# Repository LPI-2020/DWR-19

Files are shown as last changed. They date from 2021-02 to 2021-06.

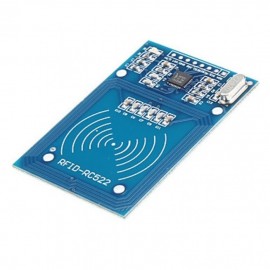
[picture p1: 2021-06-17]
01Relatorios/VariosCapitulosRelatorio/Fotos-Material/leitor-rfid-arduino.jpg

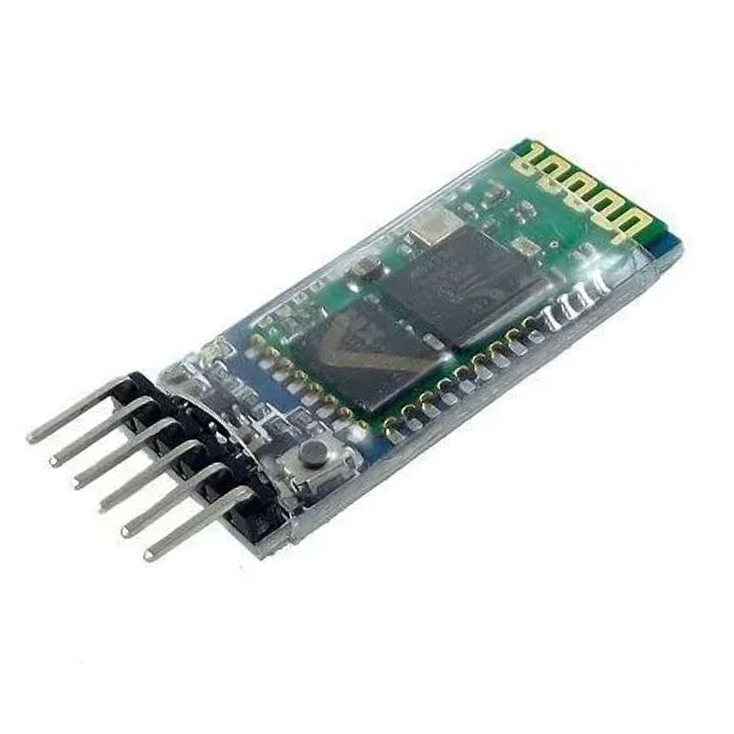
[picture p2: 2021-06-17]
01Relatorios/VariosCapitulosRelatorio/Fotos-Material/modulo_bluetooth_hc_05_mestre_escravo_341_1_20200806213305.jpg

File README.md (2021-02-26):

# Digital Waiter Robot (DWR -19)

Developed in:
- Projeto Integrador - LPI II (2021)

Members:
- Bruno Miguel Vasconcelos da Silva, a88289
- Diogo Miguel Cunha Fernandes, a88262
- Duarte Miguel Novo Rodrigues, a88259
- Francisco Lopes Salgado, a88231 
- João Pedro Dias Miranda, a88237
- José Tomás Lima de Abreu, a88218

Directed by:
- Luís André Magalhães de Barros

Short description (PT):
- A ideia do produto surgiu da necessidade de atuar perante o panorama pandémico (Covid-19), mais propriamente no auxílio a pessoas que se encontrem em isolamento.
- Uma pessoa em isolamento não pode ter contacto com o mundo exterior. Por este motivo, pensou-se em desenvolver um robô que faça chegar bens essenciais à pessoa em isolamento.
-	A função principal do produto será desempenhar o papel de um “empregado de mesa”, daí o nome “Waiter”. O termo “Digital” advém do facto de todas funcionalidades serem maioritariamente implementadas de forma digital, perfazendo o nome do robô “Digital Waiter Robot”.

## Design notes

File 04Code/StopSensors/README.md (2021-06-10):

# Stop Sensors:
- Obstacle Detector
- Cross Detector
- Room Detector

GPIO_Pins in use:
- Obstacle Detector:
ADC - triggered by timer
Ex: TIM6 (0.5sec interrupt)
    PC3 (CN9)

- Cross Detector
- Room Detector
EXTI GPIO pin A
GPIO pin B
Ex: PinA = PD0 (EXTI)(CN9)
    PinB = PD1 (CN9)

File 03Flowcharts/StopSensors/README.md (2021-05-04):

# Sensors Module

Implementation of:

- Obstacle Detector
- Crossing Detector
- Stop mark detector

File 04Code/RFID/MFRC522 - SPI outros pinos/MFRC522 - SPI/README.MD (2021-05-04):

https://github.com/xtrinch/stm32f7-demos/tree/master/07-rfid-rc522 - source code for SPI communication with MFRC522

MFRC522 RFID SPI communication module/example

Check the other Read Me file for more information on to set up this module.

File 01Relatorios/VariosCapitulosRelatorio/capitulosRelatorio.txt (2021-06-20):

- Introdução
- Arquitetura e Modulos Utilizados
DONE	- Introdução
DONE		- Diagrama de Sistema
DONE	- Sensores
DONE		- QTR, Sensor de obstáculos
DONE	- Driver
	- Módulos
		- Bluetooth, RFID
	- STM, shield
DONE	- Circuito de alimentação
DONE		- Bateria, BMS e Step-UP

- Implementação em Software
	- Introdução 
		- Máquina de estados (FSM)
	- Periféricos
	- Descrição do SW
		- Módulos criados
		- Controlador
			- Introdução ao PID
			- O que é um controlador
			- Algoritmo PID
	- Simulações ?

DONE- Lista de componentes
- Circuito mecânico
- Resultados Experimentais
- Análise do produto
	- Certificação
	- ...

- Conclusão
- Referências

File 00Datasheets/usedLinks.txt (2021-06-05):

# RFID
https://www.nxp.com/docs/en/data-sheet/MFRC522.pdf - datasheet MFRC522
https://github.com/xtrinch/stm32f7-demos/tree/master/07-rfid-rc522 - github code for spi communication with RC522
https://www.digikey.com/en/maker/projects/getting-started-with-stm32-how-to-use-spi/09eab3dfe74c4d0391aaaa99b0a8ee17 - Getting Started with STM32 - How to Use SPI

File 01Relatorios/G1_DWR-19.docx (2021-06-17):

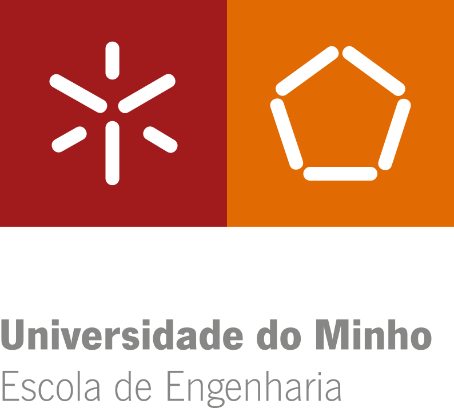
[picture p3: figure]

Bruno Miguel Vasconcelos da Silva, a88289

Diogo Miguel Cunha Fernandes, a88262

Duarte Miguel Novo Rodrigues, a88259

Francisco Lopes Salgado, a88231

João Pedro Dias Miranda, a88237

José Tomás Lima de Abreu, a88218

DWR-19

Digital Waiter Robot

Projeto integrador

Laboratórios e Práticas Integradas

Trabalho realizado sob a orientação do

Professor Luís Barros

23 junho 2021

Índice

# Lista de Figuras

# Lista de Tabelas

# Acrónimos e Siglas

Acrónimo/Sigla | Significado
DWR | Digital Waiter Robot Robô Empregado de Mesa Digital
LED | Light Emitting Diode Díodo Emissor de Luz
PWM | Pulse Width Modulation Modulação de Largura de Pulso
BMS | Battery Management System Sistema de Manutenção das Baterias
FW | Forward Para a Frente
BW | Backwards Para Trás
FWR | Forward Right Motor Direito para a Frente
FWL | Forward Left Motor Esquerdo para a Frente
BWR | Backwards Right Motor Direito para Trás
BWL | Backwards Left Motor Esquerdo para Trás
ESD | Electrostatic-Sensitive Device Equipamento Sensível à Eletricidade Estática
PCB | Printed Circuit Board Placa de Circuito Impresso
IC | Integrated Circuit Circuito Integrado
AmpOp | Amplificador Operacional
WEEE | Waste Electrical and Electronic Equipment Resíduos de Equipamentos Elétricos e Eletrónicos
MTBF | Mean Time Between Failures Período Médio Entre Falhas
f_(osc) | Frequência de Oscilação

# Capítulo 1 Introdução

## Introdução

Perante o atual panorama pandémico da Covid-19 [1] pretende-se, com a realização do Projeto Integrador da Unidade Curricular de Laboratórios e Práticas Integradas II (LPI II) do curso Mestrado Integrado em Engenharia Eletrónica Industrial e Computadores, a implementação de uma ideia com o objetivo de diminuir os contactos interpessoais que possam surgir no momento da entrega de bens a pessoas hospitalizadas. Esta situação pandémica é uma oportunidade para acelerar a transformação da área saúde.

Tendo em consideração que os hospitais tiveram um aumento considerável do número de internamentos [2], pretende desenvolver-se um produto que permita a entrega e recolha de bens essenciais de forma segura. De forma a facilitar a sua desinfeção e o seu manuseamento, o robô deverá ter superfícies lisas e uma interface simples.

A maioria das ideias nesta área tem como foco principal a saúde pública da população em geral, tais como, robôs de desinfeção [3], robôs que repõem o stock em hospitais [4] ou que medem a temperatura corporal através de câmaras [5]. Prevê-se que o Digital Waiter Robot (DWR) possa ser aplicado em contexto hospitalar. Na China construiu-se um robô (little peanut) [6] com a mesma finalidade, que foi utilizado num hotel para entregar comida porta a porta a hóspedes com suspeita de infeção.

A versatilidade do sistema permitirá que o DWR possa auxiliar na distribuição de bens noutros contextos dependendo das funcionalidades requeridas, como, por exemplo, na indústria hoteleira ou em ambiente doméstico.

## Enquadramento

O DWR é um robô seguidor de linha focado na automatização de um hospital. O DWR estará parado num local apropriado à espera do envio de um pedido e de uma rota por parte da unidade de controlo. Assim que esta conclua a comunicação com o robô, um funcionário responsável deverá colocar no seu suporte os pedidos respetivos. O robô fará chegar cada pedido a cada paciente, parando apenas nos quartos solicitados. Depois de atender a todos os pedidos, o DWR voltará ao local de onde partiu.

Considere-se o exemplo de o DWR ser responsável pela distribuição de bens alimentares. O robô deve ser colocado próximo dos locais de confeção dos alimentos. Assim que a unidade de controlo envie a rota a percorrer e as refeições a distribuir, um dos responsáveis pela secção alimentar deverá colocar estes pedidos na base do robô, dar ordem de início de marcha, e o robô tratará de tudo o resto. O DWR pode assumir outras funções, como por exemplo, na distribuição de medicamentos. A unidade de controlo poderia ser uma base de dados de gestão autónoma que tendo os dados dos quartos ocupados e dos pacientes aí hospitalizados gerisse as suas necessidades, como, por exemplo, qual a medicação prescrita, bem como o horário a que deve ser tomada. Neste projeto, implementou-se uma versão mais simples de forma a ser possível validar o conceito do robô. A unidade de controlo é uma aplicação onde, apenas, se escolhe o quarto onde o pedido deve ser entregue, e as rotas para chegar ao destino estão desde já pré-estabelecidas.

## Especificações Previstas

O DWR seguirá uma linha preta previamente colocada no piso do hospital, que define os locais acessíveis pelo robô. Como os hospitais possuem vários quartos, em vários corredores, o robô terá de ser capaz de percorrer um percurso com várias intercessões de corredores. Assim, o sistema a ser implementado será constituído por dois subsistemas: o robô DWR e a unidade de controlo. Apesar de neste projeto ser usado apenas um robô, a unidade de controlo poderá, eventualmente, controlar vários.

Como a alimentação do robô será a baterias, eventualmente, terá de ser ligado à rede elétrica para ser carregado. Assim, existirá uma estação de carregamento que estará presente num local denominado por base.

O tipo de desenvolvimento deste produto pode ser classificado como “ofensivo”. “O objetivo é colocar no mercado um produto com funcionalidades e características inovadoras ou com preço significativamente mais baixo do que produtos com funcionalidades e características equivalentes, de forma a obter para o produto quota de mercado ou aumento da quota de mercado em relação a produtos antecessores” [7].

### 1.1.1 Especificações funcionais

A unidade de controlo é responsável por uma aplicação de interface de gestão de pedidos.

Cada quarto e cruzamento no percurso deverá ter um identificador único e o DWR deve ser capaz de os detetar para que possa seguir a rota previamente estabelecida parando apenas nos quartos previstos. Após o paciente efetuar a recolha dos bens a si destinados, poderá acionar o robô de forma que este reinicie o seguimento da linha. Assim que não existam mais pedidos pendentes, o DWR retorna à base.

Para evitar que o DWR colida, este deve ter um sistema de deteção de obstáculos, que, ao detetar um objeto no seu percurso, faz com que o este pare. Se ao fim de um determinado intervalo de tempo, previamente estabelecido, a via se mantiver obstruída, deve ser emitido um sinal sonoro para alertar as pessoas ao seu redor. Se o problema for resolvido, o DWR continua o seu trajeto. Caso contrário, entrará num estado de erro e envia uma notificação para a aplicação de interface, alertando um funcionário responsável do sucedido

### 1.1.2 Especificações técnicas

Para implementação do sistema de controlo do DWR será usado um microcontrolador STM32F767ZI-NUCLEO [8], e o IDE STM32CubeIDE [9], que integra as ferramentas necessárias para a configuração de todos dos periféricos.

Para cumprir o objetivo de seguir de linha, usar-se-á um array de oito sensores de reflexão com saídas analógicas. Ao contrário dos sensores digitais que apresentam apenas dois níveis nas suas saídas, alto ou baixo, este tipo de sensores possuem uma maior sensibilidade, permitindo que o sistema de seguidor de linha apresente menos oscilações.

A deteção e identificação de intercessões de corredores será feita por meio da tecnologia RFID [11]. O sistema de deteção de obstáculos será composto por um módulo de sensores de distância infravermelhos adequado para calcular com precisão a distância a objetos que possam aparecer na frente do DWR. O sistema de alerta sonoro fará uso de um buzzer ativo. A comunicação entre o robô e a unidade de controlo será implementada recorrendo a tecnologia Bluetooth.

## Planeamento

Na Figura 1.2, mostra-se o diagrama de Gantt do planeamento inicial elaborado na etapa 0 deste projeto.

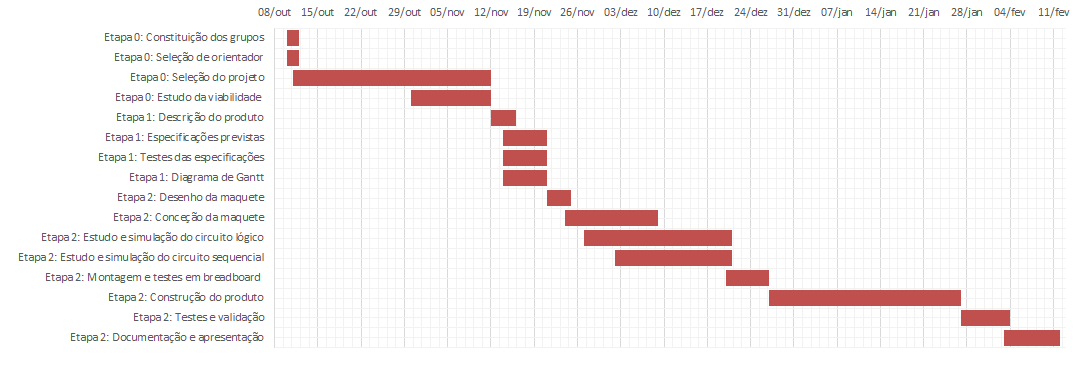
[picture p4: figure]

Figura 1.2 - Diagrama de Gantt do planeamento inicial.

Face ao confinamento geral [6], foi necessário reduzir a componente prática do projeto, nomeadamente a realização de ensaios experimentais e validação do produto. Foi feita uma análise mais cuidada do estudo da fiabilidade, segurança e certificação. A Figura 1.3 apresenta o diagrama de Gantt com as alterações efetuadas.

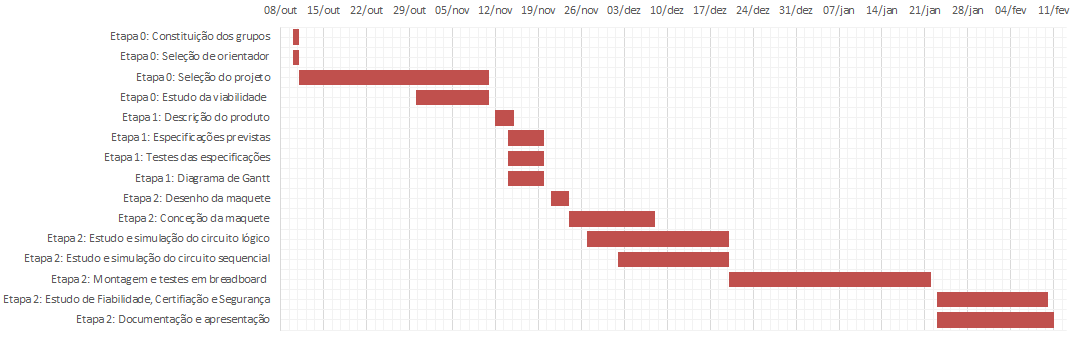
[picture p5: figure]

Figura 1.3 - Diagrama de Gantt do planeamento revisto.

# Capítulo 2 Arquitetura e Módulos Utilizados

## Introdução

## Sensores

### 2.1.1 Array de Sensores de reflexão

Para o DWR seguir a linha escolheu-se o array de sensores QTR-8A, apresentado na Figura 2.1. Este pode ser alimentado com 3,3 V ou 5 V e tem oito sensores analógicos que apresentam na sua saída um valor de tensão compreendido entre 0 V e o valor de alimentação. Sobre uma superfície branca, os sensores medem uma tensão de, aproximadamente, 0 V. Já quando se encontram sobre uma superfície preta, os sensores medem uma tensão de, sensivelmente, 3,3 V. Para as restantes cores, os sensores apresentam tensões entre estas duas gamas. No contexto deste projeto, é indispensável a escolha de um array que produza na saída uma tensão máxima de 3,3 V, uma vez que este é o limite que os analog to digital converters (ADCs) da STM32F767ZI-NUCLEO.

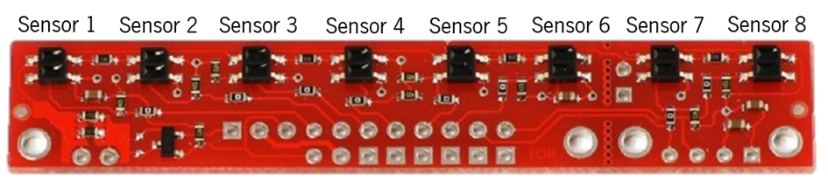
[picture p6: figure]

Figura 2.1 - Array de sensores QTR-8A.

A Tabela 2.1 apresenta a finalidade dos sensores do QTR-8A nos circuitos do DWR.

Tabela 2.1 - Sensores e sua utilização.

Sensor 1 | Sensor 2 | Sensor 3 | Sensor 4 | Sensor 5 | Sensor 6 | Sensor 7 | Sensor 8
Deteção cruzamento /quarto | - | Seguidor de linha | - | - | Seguidor de linha | - | Deteção cruzamento /quarto

### 2.1.2 Sensor de obstáculos

## Driver

Para controlo dos motores utilizou-se o módulo driver apresentado na Figura. Este driver possui seis entradas, três para cada motor: os sinais de ENA e ENB permitem ativar ou desativar os motores, controlando as suas velocidades de rotação. Por sua vez, os sinais de IN1, IN2, IN3 e IN4 definem o modo de rotação de cada motor. Na Tabela 2.2 encontra-se exemplificado o modo de operação do motor em função da combinação lógica dos sinais de entrada.

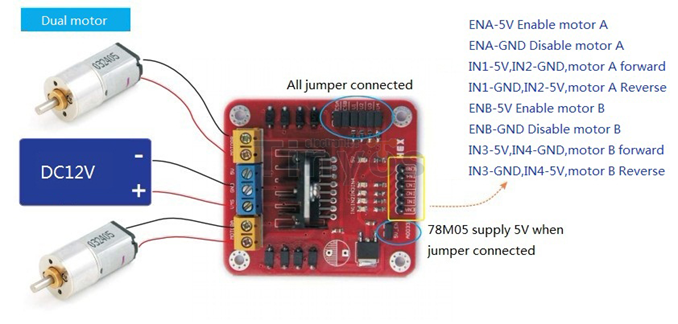
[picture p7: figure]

Figura 2.3 - Módulo Driver L298N.

Tabela 2.2 - Tabelas de verdade do driver L298N (a) Controlo do Motor A; (b) Controlo do Motor B.

(a) | (b)
ENA IN1 IN2 Motor A 0 V N/A N/A OFF 5 V 0 V 0 V Trava 5 V 0 V 5 V Sentido anti-horário 5 V 5 V 0 V Sentido horário 5 V 5 V 5 V Trava | ENB IN3 IN4 Motor B 0 V N/A N/A OFF 5 V 0 V 0 V Trava 5 V 0 V 5 V Sentido anti-horário 5 V 5 V 0 V Sentido horário 5 V 5 V 5 V Trava

## Módulos

### 2.1.3 Radio Frequency Identification (RFID)

### 2.1.4 Bluetooth

## Microcontrolador e Shield

## Circuito de Alimentação

# Capítulo 3 Implementação em Software

## Introdução

## Periféricos

### 3.1.1 Analog to Digital Converter (ADC)

### 3.1.2 Direct Memory Acess (DMA)

### 3.1.3 TIMER

### 3.1.4 Serial Peripheral Interface (SPI)

### 3.1.5 Universal Synchronous/Asynchronous Receiver/Transmitter (USART)

## Descrição de Software e Módulos Criados

## Simulações

# Capítulo 4 Lista de Componentes

Na Tabela 5.1, listam-se todos os componentes usados para o DWR, bem como a quantidade e o preço associado. É de realçar que nem todos os componentes foram adquiridos pelo preço indicado. Alguns foram emprestados, oferecidos ou adquiridos em condições mais favoráveis. No entanto, optou-se por especificar o preço de mercado.

Tabela 5.1 - Lista de componentes.

| Material | | Loja | Quantidade | Preço unitário | Preço total

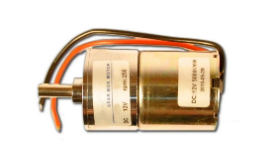
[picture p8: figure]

1 | Motor Bot'n Roll ONE 300 rpm | | Bot'n Roll | 2 | 17,50 € | 35,00 €
2 | Par de rodas Bot'n Roll ONE A (D67 mm) | | Bot'n Roll | 1 | 11,50 € | 11,50 €
3 | Par de hubs Bot'n Roll ONE A | | Bot'n Roll | 1 | 4,50 € | 4,50 €
4 | Rodas livres (D25 mm) | | Leroy Merlin | 2 | 1,69 € | 3,38 €
5 | QTR-8A | | Bot'n Roll | 1 | 19,90 € | 19,90 €
6 | Sensor Sharp 2Y0A21YK | | Bot'n Roll | 1 | 11,95 € | 11,50 €
7 | Módulo RFID RC522 | | Bot'n Roll | 1 | 4,90 € | 4,90 €
8 | Módulo Bluetooth HC-05 | | Bot'n Roll | 1 | 6,80 € | 6,80 €
9 | Módulo driver de motores L298N | | Bot'n Roll | 1 | 12,90 € | 12,90 €

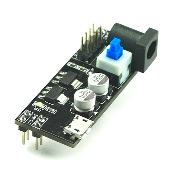
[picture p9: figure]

10 | Fonte de alimentação 5 V / 3,3 V | | Bot'n Roll | 1 | 6,5 € | 6,5 €

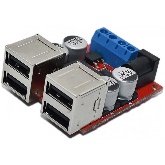
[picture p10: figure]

11 | Step-Down para UBS 5 V | | Bot'n Roll | 1 | 9,70€ | 9,70€

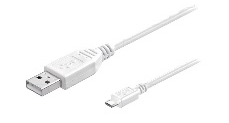
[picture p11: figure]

12 | Cabo USB A p/ micro USB B | | Bot'n Roll | 2 | 1,60 € | 3,20 €
13 | Suporte para uma pilha 18650 c/fios | | Bot'n Roll | 6 | 0,85 € | 5,10 €
14 | BMS para proteção baterias 18650 3S 12,6 V 20 A | | Bot'n Roll | 2 | 5,50 € | 11,00 €
15 | Pilha LI-ION 18650 3,7 V 2200 mAh 18X65 mm – 22 A MAX | | Bot'n Roll | 6 | 3,90 € | 23,40 €
16 | Carregador baterias 18650 | | Bot'n Roll | 1 | 8,90 € | 8,90 €
17 | Cabo DC com conector reto 9,5 mm | | Bot'n Roll | 1 | 1,70 € | 1,70 €
18 | Suporte Fusível Auto | | AlfaElektor | 1 | 1,22 € | 1,22 €
19 | Fusível Auto 3A | | AlfaElektor | 1 | 0,10 € | 0,10 €
20 | STM32F767ZI | | Bot'n Roll | 1 | 30,90 € | 30,90 €

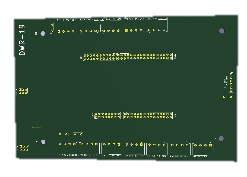
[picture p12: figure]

21 | PCB Shield STM32F767ZI | | Guimo circuito | 1 | 63,96 € | 63,96 €

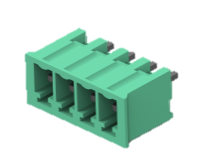
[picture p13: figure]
4P TERMIBLOK HDR DIR POL-284517-4

22 | Conectores Buchanan 284517-4 | | TE Connectivity | 12 | 1,19 € | 14,26 €

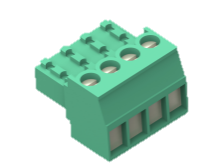
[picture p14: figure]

23 | Conectores Buchanan 284507-4 | | TE Connectivity | 12 | 2,77 € | 33,24 €

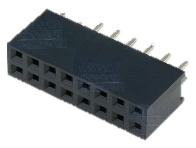
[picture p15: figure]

24 | Barra (2x8) fêmea 2,54 mm PCB | | Mauser | 1 | 0,30 € | 0,30 €
25 | Barra (2x10) fêmea 2,54 mm PCB | | Mauser | 1 | 0,40 € | 0,40 €
26 | Barra (2x16) fêmea 2,54 mm PCB | | Mauser | 1 | 0,62 € | 0,62 €
27 | Barra (2x17) fêmea 2,54 mm PCB | | Mauser | 1 | 0,69 € | 0,69 €
28 | Barra (2x3) fêmea 2,54 mm PCB | | Mauser | 2 | 0,16 € | 0,32 €
29 | Barra (1x6) fêmea 2,54 mm PCB | | Mauser | 1 | 0,09 € | 0,09 €
30 | Bloco terminal 12 conetores | | Gmlux | 1 | 0,40 € | 0,40 €
31 | Condensador poliéster | | AlfaElektor | 4 | 0,10 € | 0,40 €
32 | Botão de painel 12 mm | | Bot'n Roll | 1 | 0,60 € | 0,60 €
33 | Interruptor de painel redondo | | Bot'n Roll | 1 | 1,20 € | 1,20 €
34 | Alumínio 2 mm | | - | - | - | 35,00 €

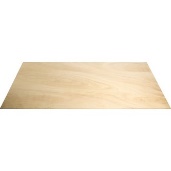
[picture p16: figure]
Placa de contraplacado 2500x1220x10mm - Leroy Merlin Portugal

35 | Placa madeira | | - | 1 | - | 5,00 €
36 | Placa de acrílico policarbonato | | - | 1 | - | 10,00 €
37 | Parafuso 4 mm | | Ferritrofa | 50 | 0,05 € | 2,50 €
38 | Parafuso 3 mm cabeça chata | | Ferritrofa | 13 | 0,05 € | 0,65 €
39 | Parafuso 6 mm | | Ferritrofa | 6 | 0,05 € | 0,30 €
40 | Parafuso 3 mm auto-roscante | | Ferritrofa | 6 | 0,04 € | 0,24 €
41 | Porca com asas 4 mm | | Ferritrofa | 8 | 0,10 € | 0,80 €
42 | Porca 4 mm | | Ferritrofa | 32 | 0,05 € | 1,60 €
43 | Porca 3 mm | | Ferritrofa | 13 | 0,05 € | 1,15 €
44 | Rebites | | Ferritrofa | 18 | 0,10 € | 1,80 €
45 | Anilhas | | Ferritrofa | 12 | 0,01 € | 0,12 €
46 | Kit Conectores 2,54 mm | | Bot'n Roll | pack | 10,95 € | 10,95 €
47 | Conjunto condutores flexíveis (1 m) | | Bot'n Roll | 4 | 1,00 € | 4,00 €
Total: | | | | | | 227,85 €

# Capítulo 5 Circuito Mecânico Implementado

(a)

(b)

(c)

(d)

(e)

Figura 6.1 - Desenho (à esquerda) e imagem real (à direita) do DWR (a) vista superior; (b) vista inferior; (c) vista lateral direita; (d) vista dianteira; (e) vista traseira.

# Capítulo 6 Resultados Experimentais

De forma a testar as especificações acima previstas, foram realizados ensaios experimentais simulando o ambiente no qual o robô irá operar.

Começou-se por testar o sensor e verificou-se que as medidas dos sensores não atingem nem 0 V nem + 5 V.

Em seguida, montou-se o circuito de atuação dos sinais PWM de modo a testar o seu funcionamento. Para isso, variou-se o sinal na entrada de feedback do TL494, através do ajuste de um potenciómetro, obtendo-se os valores de duty cycle à saída em função da tensão de entrada, como apresentado na Tabela 7.1.

Tabela 7.1 - Duty cycle do sinal PWM de saída em função da tensão de entrada.

Vcomando [V] | Duty cycle [%]
1,15 | 0
1,39 | 10
1,9 | 30
2,3 | 50
2,9 | 70
3,35 | 90
3,6 | 97

Depois de validado este circuito, ligou-se a saída deste ao driver [10] para testar a resposta do motor. Concluiu-se que o motor apenas possui binário de arranque suficiente quando o duty cycle do sinal PWM ronda os 50 %. Já com o motor em funcionamento, o duty cycle pode atingir um mínimo de 30 % sem que os motores parem. Estes dados foram retirados com os motores em vazio.

# Capítulo 7 Análise do Produto

## Introdução

Em todos os projetos práticos é necessária uma análise do produto, em áreas como a fiabilidade, segurança e certificação do sistema. Esta análise permite identificar pontos de falha do equipamento e os potenciais perigos a estes associados, de forma a informar o utilizador.

## Fiabilidade

Um sistema ou equipamento diz-se “fiável quando está livre de erros catastróficos, é capaz de recuperar de erros e apresenta resultados previsíveis (determinismo)” [15]. Apesar de, neste caso, não ser possível fazer uma avaliação do tipo quantitativa, realizou-se uma avaliação do tipo qualitativa por meio do estudo dos modos de falha e as suas consequências para o sistema e, também, influência do ambiente e do tempo.

Relativamente aos modos de falha, o desenho do sistema deve ter em conta as condições em que o robô se desvia da linha preta. Assim, este deverá ter uma velocidade adequada, uma vez que o sistema pode não responder suficientemente rápido a uma variação. Para diminuir a probabilidade de erros no seguimento da linha, deve ser favorecido o uso de linhas retas em todo o percurso e, quando necessário mudar de direção, devem ser feitas curvas ligeiras. Em acrescento, a grossura da linha deve ser ligeiramente inferior à distância entre os dois sensores usados para seguir a linha (3 cm, aproximadamente).

Do ponto de vista do ambiente que envolve o robô, devem ter-se em conta as condições climatéricas, interações com o utilizador, condições do equipamento e obstrução da via de passagem do robô. O percurso não deverá ser obstruído com objetos, sob pena de danificar tanto o robô como o objeto que o obstrui ou pessoas que se encontrem próximas, visto que o robô não possui um sistema de deteção de obstáculos. Além disso, sendo o robô um equipamento eletrónico, este não deverá estar sujeito a um ambiente húmido, tal como água ou neve, sujidade e temperaturas extremas. As condições anteriores podem provocar um mau funcionamento dos circuitos constituintes do robô, podendo, em situações extremas, danificar permanentemente o equipamento.

Em relação ao tempo de operação, sabe-se que os componentes têm um tempo médio de vida previsto pelos fabricantes. Visto que não existe informação suficiente para calcular o consumo dos circuitos do AWR, torna-se difícil fazer uma previsão do tempo de vida dos seus componentes com exatidão. Num circuito eletrónico, os componentes com maior probabilidade de falha são os condensadores, semicondutores, baterias e motores. Para quantificar o número de horas previstos de funcionamento médio de um componente, existe um parâmetro denominado Mean Time Between Failures – MTBF. Os componentes enunciados têm os MTBFs apresentados na Tabela 8.1.

Tabela 8.1 - Tempo de vida dos componentes com maior probabilidade de falha, usados no AWR.

Componente | MTBF
Baterias 18650 | 300 – 500 ciclos
Semicondutores | 10 anos
Condensadores Eletrolíticos | 11,4 anos
Condensadores Cerâmicos | 142,69 anos
Motores | 1000 a 3000 horas

Anormalidades nos circuitos poderão diminuir estes tempos consideravelmente, exigindo uma manutenção ou reparação precoce do robô.

Como calculado no subcapítulo 2.6, a autonomia prevista do robô é de uma hora e dez minutos. Caso o robô seja destinado para uso individual, desprezando o consumo dos circuitos durante o tempo de espera, e considerando, por exemplo, dez minutos como tempo de deslocação, o robô terá autonomia suficiente para transportar seis refeições. Assumindo que a cada dia existem quatro refeições (pequeno almoço, almoço, lanche e jantar), a bateria deverá ser recarregada a cada um dia e meio. Assim sendo, as baterias terão um tempo de vida útil compreendido entre um ano e três meses e dois anos e um mês, aproximadamente. Por outro lado, se o AWR for usado num âmbito coletivo, assumindo uma hora de funcionamento por refeição, a bateria deverá ser recarregada quatro vezes por dia. Calcula-se, assim, que as baterias terão de ser substituídas ao fim de dois meses e meio, podendo durar, no máximo, até quatro meses.

Conclui-se que as baterias deverão ser os elementos que requerem maior atenção, pois, além das deficiências acima apresentadas, com o aumento do tempo de utilização, estas descarregam, conduzindo a alterações dos resultados práticos.

## Segurança

A interação do robô com o utilizador deve ser realizada em segurança.

Os sistemas elétricos e fios condutores não devem estar em contacto com a armadura do robô que, sendo metálica, é condutora, evitando curto-circuitos ou choques elétricos que podem ser fatais ao sistema e prejudiciais à saúde do utilizador. Para garantir o isolamento da armadura do robô, usou-se, por questões económicas e para validação de conceitos, uma placa de madeira para suportar todos os circuitos do robô. Os motores e o array de sensores, que ficam no exterior da armadura, estão expostos ao utilizador. De forma a isolá-los eletricamente, usou-se fita isoladora envolvendo todos os terminais destes. Portanto, todos os componentes do robô estão encapsulados e isolados do utilizador. Todavia, sabe-se que este equipamento é um dispositivo sensível à eletricidade estática (frequentemente abreviado como ESD – Eletrostatic-Sensitive Device), o que significa que possui componentes que podem ser danificados por cargas elétricas estáticas que se acumulam em pessoas, ferramentas e outros materiais não condutores [16]. Se o utilizador violar o encapsulamento do produto, poderá representar perigos para este ou uma avaria no produto (Figura 8.2 (h)).

Deverá ter-se em conta que o robô possui elementos que apresentam perigos para o utilizador. A madeira usada para isolar os circuitos eletrónicos da armadura do robô é considerada um material comburente (Figura 8.2 (c)) e inflamável (Figura 8.2 (d)). Os condensadores eletrolíticos, usados nos circuitos do AWR, são componentes inflamáveis (Figura 8.2 (d)), explosivos (Figura 8.2 (e)), tóxicos (Figura 8.2 (f)) e perigosos para o ambiente (Figura 8.2 (a)). Além dos perigos associados aos condensadores, as baterias podem ser, ainda, elementos corrosivos (Figura 8.2 (b)) e comburentes (Figura 8.2 (c)). Assim, o robô não deverá estar exposto a qualquer condição ambiental extrema, tal como referido no subcapítulo anterior relacionado com a fiabilidade.

O percurso não deverá ser bloqueado por objetos, uma vez que o embate do robô poderá provocar situações imprevisíveis, com possibilidade de danificação de bens materiais ou ferimentos pessoais.

Devido aos perigos acima descritos, deve ser vigiado o manuseamento do robô por crianças.

## Certificação

Nenhum produto poderá ser exposto ao comércio antes de ser certificado. A certificação é o modo pelo qual uma entidade competente dá uma garantia escrita de que um produto está em conformidade com os requisitos especificados.

A marcação CE, apresentada na Figura 8.1, é um indicativo de conformidade obrigatória para diversos produtos comercializados no Espaço Económico Europeu. Esta marca indica que um produto respeita a legislação da União Europeia em requisitos como segurança, higiene e proteção ambiental, estando, desta forma, credenciado a circular por todo Espaço Económico Europeu [17].

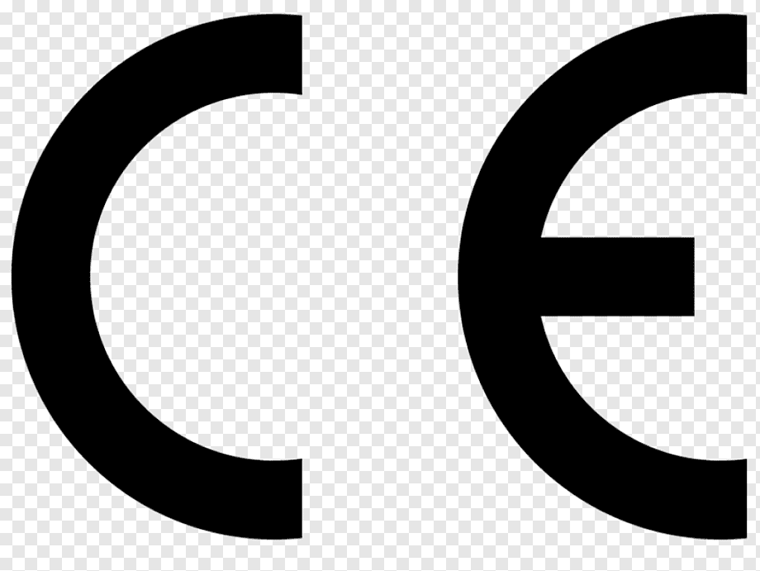
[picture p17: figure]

Figura 8.1 - Marcação CE.

De acordo com DIRETIVA 2014/35/UE [18] ANEXO I, que informa os principais elementos dos objetivos de segurança para o material elétrico usado no equipamento, devem ser previstas medidas de ordem técnica a fim de que:

a) As pessoas e os animais domésticos fiquem protegidos de forma adequada contra os riscos de ferimentos ou de outros acidentes resultantes de contactos diretos ou indiretos;
b) Não se produzam temperaturas, descargas ou radiações que possam provocar perigo;
c) As pessoas, os animais domésticos e os bens sejam protegidos de forma adequada contra os riscos de natureza não elétrica provenientes do material elétrico que a experiência venha a revelar;
d) O isolamento seja adequado aos condicionamentos previstos.

Como já foi apresentado, o robô cumpre com os pontos a), b) e d). Uma vez que este projeto serve fins académicos, ou seja, tem o propósito de validar conceitos, não foi implementado um sistema de deteção de obstáculos. Assim, o ponto c) não é cumprido, pelo que o certificado CE não poderá ser atribuído ao AWR.

Devido aos perigos enunciados no subcapítulo anterior, relacionado com a segurança, deverão ser apresentados vários símbolos ao utilizador.

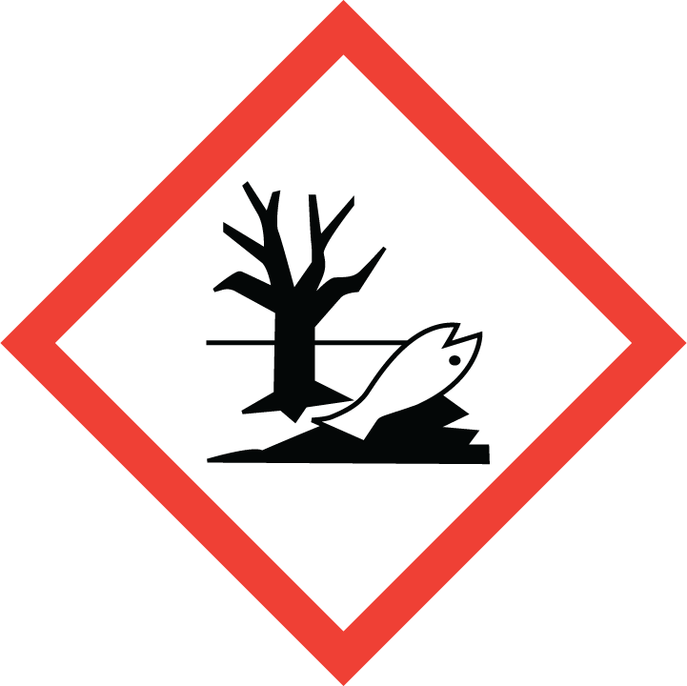
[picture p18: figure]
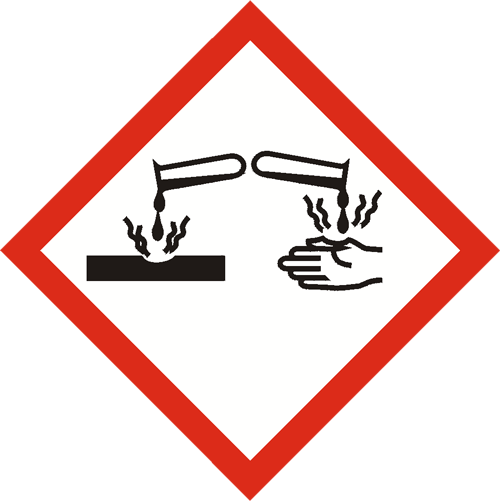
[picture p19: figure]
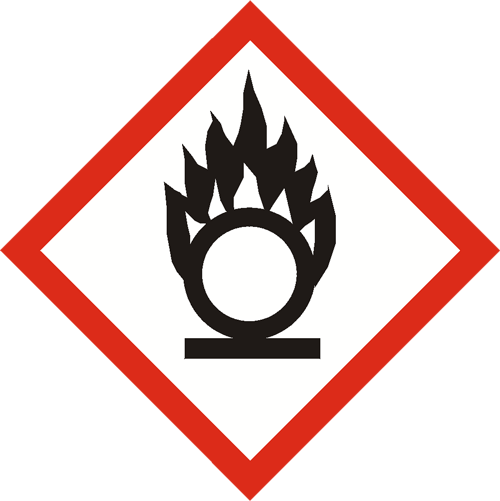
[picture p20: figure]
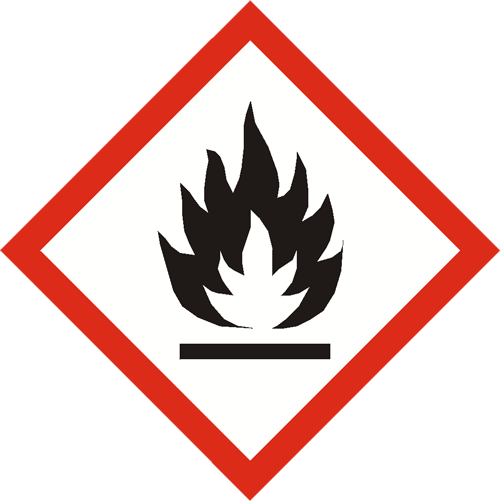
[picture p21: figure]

(a) | (b) | (c) | (d)

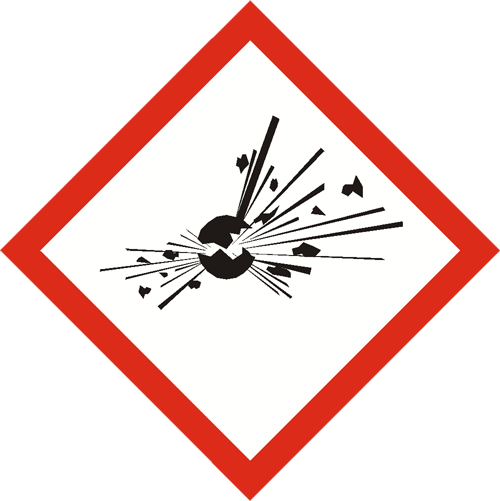
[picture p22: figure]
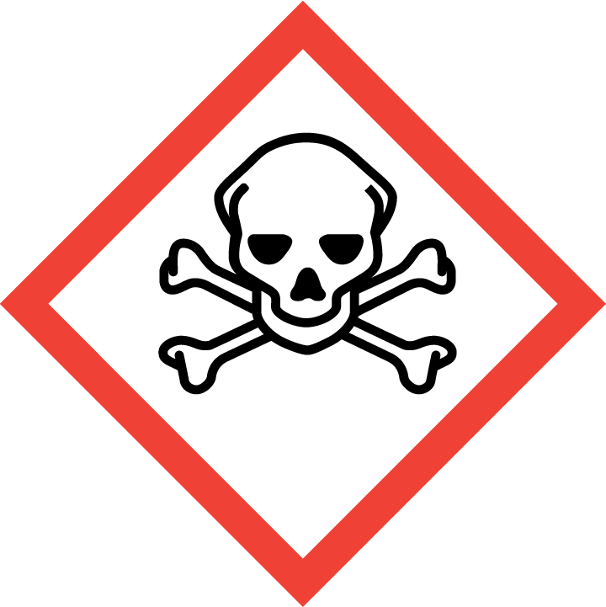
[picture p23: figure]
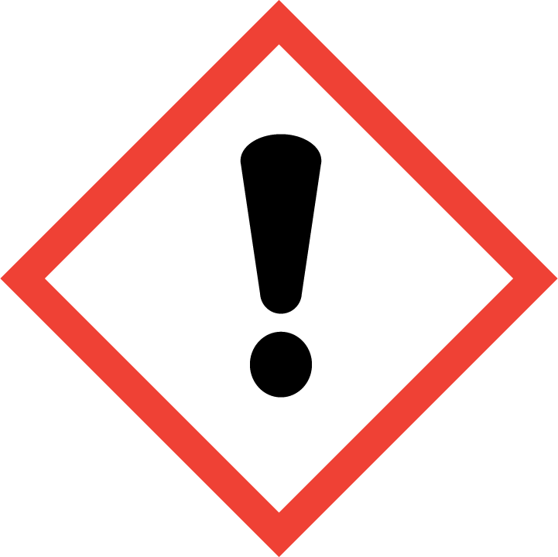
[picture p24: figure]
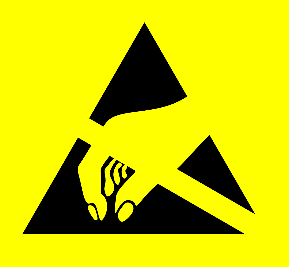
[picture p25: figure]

(e) | (f) | (g) | (h)

Figura 8.2 - Símbolos de perigo: (a) perigoso para o ambiente; (b) corrosivo; (c) comburente; (d) inflamável; (e) explosivo; (f) tóxico; (g) vários perigos; (h) Eletrostatic Sensitive Device - ESD.

O robô será constituído por circuitos e componentes eletrónicos que não podem ser enviados para o lixo doméstico. Estes devem ser encaminhados para locais próprios de reciclagem (Figura 8.3).

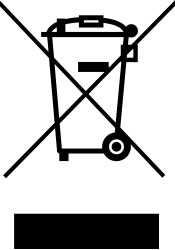
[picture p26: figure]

Figura 8.3 - Símbolo WEEE.

# Capítulo 8 Conclusões

## Conclusão

O projeto integrador da unidade curricular de LPI I pôs à prova algumas competências adquiridas ao longo do curso. Aplicaram-se conhecimentos das unidades curriculares de Sistemas Digitais, Eletrónica I e II, Instrumentação e Sensores, Controlo Automático, Máquinas Elétricas, entre outras. Foi um projeto ímpar comparativamente a projetos já realizados porque envolveu um maior conhecimento de várias áreas e requereu muito trabalho autónomo.

Ao longo do design e testes do robô foram encontrados vários problemas, que provocaram alterações na forma como se abordou o desenvolvimento do projeto. Inicialmente usou-se o sensor de linha no centro do robô de forma a facilitar a inversão do sentido de marcha no final do seu trajeto, evitando assim que o robô necessitasse de efetuar uma volta de 180 ° sobre o seu eixo. Assim, os motores teriam de rodar num sentido quando o robô fosse na direção do paciente, e no sentido contrário quando tivesse de voltar ao ponto de partida, simplificando a lógica que controla o estado de funcionamento do robô. Foram implementadas e testadas diversas soluções que não cumpriram o seu propósito, pois, durante a realização de testes, verificou-se que esta abordagem revela problemas mecânicos. Desta forma, o ponto central do robô (posição do sensor) é menos sensível a alterações de direção, aumentando o seu tempo de resposta, impedindo-o de seguir a linha corretamente. Após a alteração da posição do sensor para a dianteira do robô, estes problemas resolveram-se.

Relativamente ao desenho e implementação da máquina de estados, também se encontraram dificuldades. Inicialmente, não houve a preocupação de selecionar integrados da mesma família lógica, para implementar a máquina de estados, o que originou resultados indefinidos. Verificou-se que todos os integrados devem ser da mesma família lógica, ou compatíveis com a lógica TTL, sendo possível obter posteriormente resultados mais próximo dos desejados quanto utilizada a família HCT [10].

Infelizmente, não foi possível aprofundar nem testar todas as funcionalidade previstas para o projeto, devido ao confinamento geral [6]. O planeamento inicial vinha a ser cumprido até que as circunstâncias mudaram e alguns dos objetivos propostos não puderam ser realizados.

Relativamente ao tempo despendido no desenvolvimento do projeto, visto que todo o grupo se juntou para trabalhar em horários definidos, todos os elementos do grupo trabalharam o mesmo número de horas. Após o desenho e conceção que foi desenvolvido em conjunto, o grupo foi dividido em duas equipas de trabalho, sendo que uma se dedicou à implementação do controlo dos motores e outra ao desenvolvimento da máquina de estados que controla o estado de funcionamento do robô. Assim, foram contabilizadas, individualmente, um total de 250 horas, como mostrado na Tabela 9.1.

Tabela 9.1 - Número de horas despendidas por elemento

Nome | Número de Horas
Bruno Silva | 250
Diogo Fernandes | 250
Duarte Rodrigues | 250
Francisco Salgado | 250
João Miranda | 250
José Abreu | 250

Em suma, este projeto foi desafiante, revelando a sua importância na formação enquanto futuros engenheiros.

## Sugestões de Trabalho Futuro

Durante a realização deste projeto, foram feitas opções que ditaram um rumo. Poder-se-iam ter tomado outras opções que modificariam os resultados obtidos. Este projeto não representa o fim de uma ideia, é, apenas, uma implementação de um conceito. Assim, neste subcapítulo são feitas algumas sugestões de, não só, melhorias à implementação desenvolvida, mas também de novas abordagens para esta ideia.

### Possíveis Opções Alternativas para o Desenho dos Circuitos

Todos os projetos são passíveis de melhorias. Sendo um projeto totalmente analógico, algumas melhorias não terão uma implementação tão simples e barata quando comparadas com uma implementação digital.

Tal como implementado, não existe nenhum mecanismo de deteção caso o robô saia fora da rota. Uma possível melhoria para a resolução deste problema seria usar um ou dois dos sensores centrais do array de sensores para deteção da linha. Caso esta não fosse detetada, o robô teria de parar, evitando que este ande indefinidamente.

Outro aspeto a melhorar seria a implementação de um mecanismo de deteção de obstáculos. Caso o robô se encontrasse sobre a linha e um objeto obstruísse a sua passagem, este teria de parar de forma a evitar a colisão e possíveis danos materiais de ambas as partes. Além disso, o robô deveria emitir um som intermitente de forma a alertar o responsável pelo sucedido. Este mecanismo poderia ser implementado através de um sensor de proximidade colocado na dianteira do robô. Sem este sistema, o robô embaterá no objeto, provocando um comportamento indefinido.

Tendo em conta que o objetivo deste robô é minimizar os contactos possivelmente infeciosos com outras pessoas, seria relevante implementar uma interface diferente com o utilizador. Ao invés de fazer uso de um botão de pressão para iniciar a marcha, seriam usadas células de carga que detetam a colocação de um tabuleiro sobre o robô. Assim que o utilizador ou operador colocassem o tabuleiro sobre o robô, após o término de um temporizador, este iria iniciar a marcha, minimizando os contactos com a armadura do robô. Além disso, poderia ser desenvolvido um sistema automático de desinfeção das superfícies do robô, que deveria ser acionado após finalizar o seu percurso (ida e volta).

Como o robô funciona à base de baterias, estas poderiam ser recarregadas numa estação de carregamento. Para isso, poderia ser desenvolvida uma estação de carregamento onde se colocaria o robô, sempre que não estivesse em utilização.

Tal como foi visto, apontaram-se apenas algumas formas de melhorar o trabalho desenvolvido. Possivelmente, existirão outras melhorias a serem aplicadas e que não foram abordadas neste capítulo. No entanto, algumas seriam descartadas por não justificarem o trabalho, terem uma execução complexa para o efeito ou não serem economicamente viáveis.

### Evolução do Atual Desenho para um Sistema Baseado em Microcomputador

O atual desenho do robô poderia ser implementado num sistema baseado em microcomputador, tal como será visto na unidade curricular de Laboratórios e Práticas Integradas II (LPI II).

Como o propósito do robô é fazer chegar bens a alguém que se encontre numa situação de isolamento, o seu aspeto físico seria idêntico ao implementado.

Através do uso de um microcomputador, existirão múltiplas possibilidades de implementação. Uma delas seria o uso do controlo remoto, através do qual uma pessoa responsável controlaria o percurso do robô até ao local pretendido. Teria de ser adicionada uma câmara ao robô, sendo a imagem transmitida para o comando, ou algum dispositivo eletrónico com ecrã, que o utilizador estivesse a utilizar. Este sistema poderia ser implementado através da tecnologia Bluetooth, em que o robô seria controlado por um smartphone. Outra possibilidade seria a criação de rotas pré-definidas para o robô seguir. Fazendo uso de sensores de distância, o robô poderia desviar-se de obstáculos que se encontrassem na sua rota. Além disso, o robô poderia estimar se teria carga suficiente nas baterias de modo a conseguir completar a trajetória pretendida. Caso não se verificasse, dirigir-se-ia automaticamente à sua estação de carregamento.

A solução que mais se assemelha à implementação atual, seria fazer o uso do microcomputador para seguir uma linha preta, através do array de sensores [19] e implementar as funcionalidades referidas no capítulo anterior.

Neste subcapítulo apenas foram apresentadas algumas possibilidades, sem idealizar a sua implementação ou grau de complexidade. Assim, no próximo semestre, na unidade curricular de LPI II, será avaliada a viabilidade de todas as ideias acima referidas.

# Referências

[1] SNS - Serviço Nacional de Saúde, “Covid-19 | Pandemia,” 11 março 2020. [Online]. Available: https://www.sns.gov.pt/noticias/2020/03/11/covid-19-pandemia/. [Acedido em 16 dezembro 2020].

[2] “Conheça Jaci: o robô de desinfecção que auxilia no combate a Covid-19,” Tecnopuc, 29 abril 2020. [Online]. Available: https://www.pucrs.br/tecnopuc/2020/04/29/conheca-jaci-o-robo-de-desinfeccao-que-auxilia-no-combate-covid-19/. [Acedido em 8 fevereiro 2021].

[3] E. L. Brand Talk, “Pandemic and the Smarter World: A Future of Robots?” 5 maio 2020. [Online]. Available: https://www8.gsb.columbia.edu/articles/brand-talk/pandemic-and-smarter-world-future-robots. [Acedido em 10 fevereiro 2021].

[4] R. K. Erico Guizzo, “How Robots Became Essential Workers in the COVID-19 Response,” IEEE SPECTRUM, 30 setembro 2020. [Online]. Available: https://spectrum.ieee.org/robotics/medical-robots/how-robots-became-essential-workers-in-the-covid19-response. [Acedido em 10 fevereiro 2021].

[5] J. D'Onfro, “Robots To The Rescue: How High-Tech Machines Are Being Used To Contain The Wuhan Coronavirus,” 2 fevereiro 2020. [Online]. Available: https://www.forbes.com/sites/jilliandonfro/2020/02/02/robots-to-the-rescue-how-high-tech-machines-are-being-used-to-contain-the-wuhan-coronavirus/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. [Acedido em 16 dezembro 2020].

[6] P. Semiconductors, “74HCT14 Hex inverting Schmitt trigger”. 74HCT14 datasheet, 26 agosto 1997 [revisto a 30 outubro 2003].

[7] T. Instruments, “TL494 Pulse-Width-Modulation Control Circui”. TL494 datasheet, janeiro 1983 [revisto a março de 2017].

[8] STMicroelectronics, “DUAL FULL-BRIDGE DRIVER”. L298 datasheet, janeiro 2000.

[9] Texas Instruments, “SN54/74HCT CMOS Logic Family Applications and Restrictions,” maio 1996. [Online]. Available: https://www.ti.com/lit/an/scla011/scla011.pdf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. [Acedido em 2 fevereiro 2021].

[10] T. Corporation, “TENERGY 18650 2200 mAh Li-Ion Cell”. Tenergy 18650 datasheet.

[11] “BMS PARA PROTECÇÃO BATERIAS 18650 3S 12,6V 20A,” [Online]. Available: https://www.botnroll.com/pt/acessorios/2558-bms-para-protec-o-baterias-18650-3s-12-6v-20a.html. [Acedido em 10 fevereiro 2021].

[12] Z. Electromotor. ZGB37RG datasheet.

[13] T. Instruments, “LM340, LM340A and LM78xx Wide VIN 1.5-A Fixed Voltage Regulators”. LM7805 datasheet, setembro 2000 [revisto a julho de 2016].

[14] P. Carvalhal, “Fiabilidade e boas práticas de projeto,” 2014. [Online]. Available: https://elearning.uminho.pt/bbcswebdav/pid-1045855-dt-content-rid-3987823_1/courses/2021.9305O4_1/FiabilidadeBoasPraticasProjeto_PCarvalhal.pdf. [Acedido em 3 fevereiro 2021].

[15] “Electrostatic-sensitive device,” Wikipedia, [Online]. Available: https://en.wikipedia.org/wiki/Electrostatic-sensitive_device. [Acedido em 8 fevereiro 2021].

[16] TUR CERT, “O que é o certificado CE?” [Online]. Available: https://www.ceisaret.com/pt/ce-sertifikasi-nedir/. [Acedido em 2 fevereiro 2021].

[17] Jornal Oficial da União Europeia, “DIRETIVA 2014/35/UE DO PARLAMENTO EUROPEU E DO CONSELHO,” 29 março 2014. [Online]. Available: https://eur-lex.europa.eu/legal-content/PT/TXT/PDF/?uri=CELEX:32014L0035&from=EN. [Acedido em 8 fevereiro 2021].

[18] A. G. e. I. Cardoso, “Fecha tudo. Escolas e universidades em casa a partir de sexta-feira.,” Jornal de Notícias, 21 janeiro 2021. [Online]. Available: https://www.jn.pt/nacional/fecha-tudo-escolas-e-universidade-em-casa-a-partir-de-sexta-feira-13256762.html. [Acedido em 3 fevereiro 2021].

[19] P. Corporation, “pololu.com,” 2001-2014. [Online]. Available: https://www.pololu.com/docs/pdf/0J12/QTR-8x.pdf. [Acedido em 3 fevereiro 2021].

[20] G. Bocock, “Electrolytic Capacitors Determine The Lifetime Of A Power Supply,” XP Power, [Online]. Available: https://www.xppower.com/resources/blog/electrolytic-capacitor-lifetime-in-power-supplies. [Acedido em 11 fevereiro 2021].

[21] “How can I estimate the life of ceramic capacitors?” Taiyo Yuden, [Online]. Available: https://www.yuden.co.jp/eu/product/support/faq/q020.html. [Acedido em 11 fevereiro 2021].

[22] “How to Prolong the Life of an 18650 Battery,” instructables ciruits, [Online]. Available: https://www.instructables.com/How-to-Prolong-the-Life-of-an-18650-Battery/. [Acedido em 11 fevereiro 2021].

[23] A. Perzan, “Brushed vs. brushless DC motors,” drive.tech, [Online]. Available: https://drive.tech/en/stream-content/brushed-vs-brushless-dc-motors. [Acedido em 11 fevereiro 2021].

[24] T. Instruments, “Calculating Useful Lifetimes of Embedded Processors,” 2014. [Online]. Available: https://www.ti.com/lit/an/sprabx4b/sprabx4b.pdf?ts=1612984192026. [Acedido em 11 fevereiro 2021].

Capítulo 9 - Conclusões

Capítulo 5 – Circuito Mecânico Implementado

Capítulo 6 – Resultados Experimentais

Capítulo 7 – Análise do Produto

Capítulo 8 - Conclusões

Lista de Figuras

Lista de Tabelas

Acrónimos e Siglas

Capítulo 1 - Introdução

Capítulo 2 –Arquitetura e Módulos Utilizados

Capítulo 3 – Implementação em Software

Capítulo 4 – Lista de Componentes

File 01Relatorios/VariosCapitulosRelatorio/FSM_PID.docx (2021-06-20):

Máquina de Estados

O DWR tem de executar ações distintas durante toda a sua atividade. De forma a ser possível executar a ação correta em todos os momentos, é necessário um sistema que faça a gestão do estado atual do robô e das entradas que possam despoletar a alteração deste mesmo estado. Na fig x, está representado o diagrama que representa a máquina de estados implementada para este robô. Esta é composta por quatro estados principais: S_STOPPED, S_RECEIVE, MOVEMENT e S_ERROR. O estado de MOVEMENT pode ser subdividido em quatro estados secundários: S_FLW_LINE, S_RD_RFID, S_NEXT_MOV e S_ROTATE.


Legenda: Diagrama da máquina de estados.

Inicialmente, o DWR encontra-se no estado S_STOPPED e transita para o estado S_RECEIVE quando a rota atual estiver terminada e o operador iniciar a transmissão de uma nova rota. Após receber a rota selecionada pelo operador na aplicação, o robô transita do estado S_RECEIVE para o estado S_STOPPED, onde espera que lhe seja dada a permissão para iniciar o seu movimento, através da pressão do botão presente na sua lateral. Assim que este botão seja pressionado, o sistema evolui para o estado de S_FLW_LINE. Neste estado o robô segue a linha até que aconteça algum dos seguintes imprevistos: presença de um obstáculo no percurso do robô, deteção de uma cruz de paragem (quarto ou cruzamento) ou ocorrência de falha no controlador do seguidor de linha. Caso o percurso esteja obstruído por um obstáculo, o DWR para, evitando a colisão com o mesmo, voltando para estado S_STOPPED. Se for detetada uma linha horizontal por ambos os sensores das extremidades do array de sensores (cruz de paragem), significa que o robô está na presença de um quarto ou cruzamento, sendo necessário efetuar a leitura do cartão RFID a este associado, no estado S_RD_RFID. Caso o cartão RFID seja lido com sucesso, o sistema evolui para o estado S_NEXT_MOV, onde determina qual o próximo estado do DWR, de acordo com a rota selecionada. No estado S_NEXT_MOV, o robô transita para o estado S_FLW_LINE se o RFID detetado for relativo a um quarto que não esteja marcado como local de paragem na rota ou a um cruzamento em que não seja necessário efetuar a mudança de direção. Pelo contrário, caso seja necessário efetuar paragem no quarto atual, dá-se uma transição para o estado S_STOPPED. No caso do RFID detetado ser relativo a um cruzamento e for necessário mudar de direção, o sistema transita para o estado S_ROTATE. Uma vez neste estado, o DWR roda na direção indicada pela rota, até estar orientado na direção pretendida, voltando ao estado S_FLW_LINE.

Todas estas ações têm timeouts associados, que são ativos quando a ação demora mais tempo a ser realizada do que o esperado, permitindo ter controlo sobre o robô em casos imprevisíveis, transitando para o estado S_ERROR, por exemplo, quando o DWR se encontrar parado à espera de que o percurso seja desobstruído por um longo período de tempo, quando ocorre um erro (cartão errado ou demasiado tempo) na leitura de um cartão RFID ou quando ocorre um erro na mudança de direção do robô. Além disso, o robô transita para o estado S_ERROR quando o robô sai totalmente da linha durante o seu percurso. Uma vez neste estado, o DWR precisa da intervenção de um responsável para que possa voltar ao seu estado de funcionamento normal.

O que é um Controlador

Um controlador é responsável pelo controlo de processos através de algoritmos específicos. O seu principal objetivo consiste na monitorização, identificação e interpretação de processos, via modelos matemáticos, de forma a produzir uma ação de controlo conveniente. Existem três ações de controlo distintas: proporcional, integral e derivativa, que podem ser conjugadas entre si. A primeira tem uma ação imediata, proporcional ao valor atual do erro, acelera a resposta de um processo controlado, reduz o tempo de subida e o erro máximo. No entanto, aumenta o overshoot, o tempo de estabilização e produz um offset inversamente proporcional ao ganho. A ação integral produz uma ação de controlo gradual proporcional à integral do erro, respondendo, assim, ao passado do erro enquanto este for diferente de zero, elimina o offset e reduz o tempo de subida. Porém, aumenta o overshoot, o período de oscilação e tempo de estabilização, produzindo respostas lentas e oscilatórias. A ação derivativa produz uma ação antecipatória e proporcional à derivada do erro. É usada para acelerar e estabilizar a malha, reduzir o overshoot, o erro máximo e o período de oscilação. Contudo, não é indicada para processos com ruído.

Na Figura, estão presentes as três ações de controlo descritas. A figura (a) mostra a resposta de um sistema a uma ação proporcional. A saída deste corresponde à variável de erro multiplicada por uma dada constante. A figura (b) mostra a resposta de um sistema a uma ação integral, onde a saída deste corresponde à integral da variável de erro. Como a integral de uma constante é uma reta, quando a entrada (variável de erro) é do tipo degrau, a resposta do sistema vai corresponder a uma rampa de declive igual à amplitude da variável de entrada multiplicada por uma constante. A figura (c) mostra a resposta de um sistema a uma ação derivativa, em que a saída deste corresponde à derivada da variável de erro. Como a derivada de uma reta é uma constante, quando a entrada é do tipo rampa, a saída do sistema corresponde a um degrau de amplitude igual à amplitude da rampa multiplicada por uma constante. Um controlador que conjugue as três ações é denominado por controlador proporcional integral derivativo (PID).


(a) | (b) | (c)

Análise do sistema do controlo

O primeiro passo num projeto de controlo está relacionado com a compreensão qualitativa do sistema. É necessário compreender como o sistema a controlar funciona fisicamente, quais as variáveis medidas, a controlar, de atuação, distúrbio e comando, bem como o funcionamento dos atuadores, sensores e controlador.

O sistema a ser controlado assemelha-se a um paralelepípedo com uma roda posicionada na parte central de cada lateral do robô. Sendo o objetivo do sistema seguir uma linha, que pode conter trajetórias retas ou curvilíneas, a velocidade de rotação dos motores terá de variar de modo a ser possível ajustar as velocidades de translação e de rotação do centro de massa do robô. Se se pretender que o robô siga uma trajetória retilínea, os motores terão de rodar à mesma velocidade. Se se pretender que o robô efetue uma trajetória curvilínea, o motor do lado oposto ao que se pretende efetuar a trajetória terá de ter uma velocidade de rotação superior. Ou seja, quando a trajetória é uma curva à esquerda, o motor do lado direito terá de ter uma velocidade de rotação superior comparativamente com a do motor do lado direito. Quando a trajetória é uma curva à direita, passa-se o oposto.

As variáveis medidas são as leituras efetuadas pelos dois sensores do seguidor de linha, o sensor 3 e o sensor 6 (ref imagem do qtr). As variáveis a controlar são a velocidade de translação e velocidade de rotação do centro de massa do robô. As variáveis de atuação são os binários dos motores. As variáveis de comando são a fração de modulação do amplificador PWM de cada motor. A variável de perturbação será o atrito provocado pela superfície (binário de perturbação).

O atuador é composto pelo motor DC (ref), a ponte H(ref) e pelo microcontrolador(ref). O binário produzido pelo motor DC pode ser alterado através da variação da tensão de alimentação do motor (produzida por um amplificador PWM).

O sistema de controlo é responsável pela variação deste parâmetro, de maneira a produzir o binário adequado à velocidade requerida para que o DWR siga a linha corretamente. Em conjunto, o microcontrolador e a ponte H implementam o amplificador PWM. O algoritmo de controlo implementado no microcontrolador produzirá na saída a variável de comando, a fração de modulação do amplificador de PWM, sendo o ganho deste amplificador correspondente a tensão aplicada ao motor DC quando a fração de modulação é um.

O controlador é efetuado através do microcontrolador. A regra de controlo executada por este controlador está implementada numa rotina de serviço à interrupção (ISR), que será despoletada por um timer com período igual ao período de amostragem escolhido pelo sistema de controlo. Esta ISR terá como parâmetros de entrada os valores das leituras dos dois sensores a utilizar e como saída a fração de modulação de PWM, que servirá de entrada aos amplificadores PWM.

Na Figura, está ilustrado o sistema de controlo implementado. Sendo o objetivo principal do DWR o seguimento de uma linha, é necessário manter os sensores na parte exterior da mesma. Quando um dos sensores se aproximar da linha, o motor do lado oposto terá de compensar o desvio da trajetória. Pretende-se que a diferença entre as leituras dos dois sensores, ou seja, a variável de erro, seja nula, portanto, conclui-se que a variável de referência tem o valor zero.

Se o valor de erro for positivo, significa que o sensor esquerdo se encontra mais próximo da linha do que o sensor direito, implicando que o motor direito tenha uma velocidade de rotação superior. À variável de saída do bloco controlador PID soma-se um valor de offset que servirá de variável de comando para o atuador direito (driver motor e motor). Ao simétrico da variável de saída do bloco PID soma-se o mesmo valor de offset, que servirá de variável de comando para o atuador esquerdo (driver motor e motor). Deste modo, o valor da variável de comando do atuador direito é superior ao valor da variável de comando do atuador esquerdo.

Se o valor do erro for negativo, passa-se o oposto. Se a variável de saída do controlador PID for nula não é necessário fazer ajustes de direção e o DWR seguirá o percurso com velocidade de rotação constante em ambos os motores, com valor igual ao valor de offset.


Adicionar cores aos blocos deste diagrama, como já se fez para o AWR. Escrever “variável de comando para o motor direito” e “variável de comando para o motor esquerdo”, em vez de “Variável de comando” para os dois? O mesmo para a variável de atuação? Erro -> Variável de erro: Panta -> DWR???? Trocar mais com menos a saída do PID

Controlador Implementado

Bloco PID

Um controlador PID contínuo é definido pela Equação, em que k_p , k_i e k_d são referidos, respetivamente, como os ganhos proporcional, integral e derivativo, e e(t) como a variável de erro ao longo do tempo. A variável de comando, u(t) , corresponde ao somatório das ações proporcional, integral e derivativa.

| u(t)=k_p e(t)+k_i ∫_0^t e(t^(') ) dt^(') + k_d (de(t))/(dt) | (2.4)

Para uma implementação em microcontrolador é necessária uma versão digital do controlador. De entre as diversas famílias das regras PID implementou-se o algoritmo de posição. Esta versão consiste em substituir os termos integral e derivativo, da equação acima xx, pelos seus equivalentes discretos: soma e a diferença divida de 1ª ordem, respetivamente. Assim, obtém-se a Equação, em que u[n] e e[n] são, respetivamente, a ação de controlo e o erro no instante n . Em cada instante é calculado o valor real (de posição) do sinal de saída do controlador. No contexto do problema, a variável de erro corresponde à diferença entre as leituras dos dois sensores, aqui representados, simbolicamente, por IN_1 e IN_2 (Equação).

| u[n]=k_p e[n]+k_i ∑_(k=0)^(n-1) e[k]+ k_d [e[n]-e[n-1]] | (2.4)
| e[n]=IN_1 -IN_2 | (2.4)

Para efeitos de cálculo, o valor de u[n] pode ser escrito de forma mais adequada, calculando o erro apenas uma vez e colocando em evidência as constantes na aproximação à integral e à derivada (Equação). Pode-se agora redefinir os ganhos proporcional, integral e derivativo (Equação) obtendo-se, por substituição, a Equação.

| u[n]=(k_d)/h [e[n]-e[n-1]]+k_p e[n]+k_i h∑_(k=0)^(n-1) e[k] | (2.4)
| k_(ph) =k_p | (2.4)
| k_(ih) =k_i h | (2.4)
| k_(dh) =(k_d)/h | (2.4)
| u[n]=k_(dh) [e[n]-e[n-1]]+k_(ph) e[n]+k_(ih) ∑_(k=0)^(n-1) e[k] | (2.4)

Para calcular o somatório dos erros, presente na Equação, define-se a variável sum_e [n] (Equação) que pode ser escrita de forma recursiva (Equação). Juntando todas as transformações efetuadas, obtém-se, na Equação, uma nova versão da expressão inicial (Equação).

| sum_e [n]=∑_(k=0)^(n-1) e[k] | (2.4)
| sum_e [n]=sum_e [n-1]+e[n-1] | (2.4)
| u[n]=k_(dh) [e[n]-e[n-1]]+k_(ph) e[n]+k_(ih) sum_e [n] | (2.4)

Uma forma de reduzir os problemas com erros de medida prende-se com a utilização de um filtro passa-baixo na ação derivativa. Na Equação apresenta-se a expressão desta ação. Calculando a sua transformada em Z obtém-se a Equação. A aproximação à derivada introduz um zero em z=1 e um polo em z=0 , no plano Z . Pode-se deslocar o polo para a direita, no plano Z , com um filtro passa-baixo resultando as Equações. A função de transferência tem um zero em z=1 , como no caso anterior, mas o polo acentua-se em z=a , e não em z=0 . A implementação desta função de transferência está representada na Equação. Pode-se então redefinir k_(dh) como apresentado na Equação. Adicionando a componente do filtro passa-baixo Equação chega-se à Equação. A segunda reduz-se à primeira se a for zero, ou seja, a ação derivativa sem filtro de passa-baixo é obtida com a=0 , o que implica que k_(dh) =k_d /h .

| u_d [n]=(k_d)/h(e[n] - e[n-1]) | (2.4)
| U_d (z)=k_d (z-1)/(h z) E(z) | (2.4)
| U_d (z)=k_d ((1-a)z)/(z-a)(z-1)/(h z)E(z) | (2.4)
| U_d (z)=(k_d (1-a))/h(z-1)/(z-a)E(z) | (2.4)
| U_d (z)=(k_d (1-a))/h(1-z^(-1))/(1-az^(-1))E(z) | (2.4)
| u_d [n]=a u_d (k-1)+(k_d (1-a))/h[e[n]-e[n-1]] | (2.4)
| k_(dh) =(k_d (1-a))/h | (2.4)
| u[n]=k_(ph) e[n]+k_(ih) sum_e [n]+a u_d (k-1)+k_(dh) [e[n]-e[n-1]] | (2.4)

Um dos problemas de algoritmo de posição está relacionado com a possível saturação do valor de u. Definem-se, então, limites de saturação superior ( U_(sata) ) e inferior ( U_(satb) ). Se o resultado do cálculo do valor de u for superior ao valor do limite de saturação superior, ou inferior ao valor do limite de comparação inferior, é necessário limitar o mesmo aos valores de saturação impostos. Assim, modifica-se a interrupção para detetar a ultrapassagem dos valores de saturação e, caso tal aconteça, fixa-se o valor de u nos valores de saturação. Além disso, a saturação do atuador pode dar origem a um aumento brusco dos valores dos somatórios dos erros levando a oscilações prejudiciais no valor da variável controlada.

Tendo em conta os aspetos mencionados acima e fazendo uso da Equação é possível desenhar o fluxograma que permite a implementação do algoritmo de controlo no microcontrolador, Figura. Como se pode verificar, a atualização do somatório dos erros só é efetuada quando a variável u se encontra dentro dos limites de saturação. Caso contrário, a atualização é anulada, o que equivale, em tempo contínuo, a parar a integração do erro, fixando-se o valor de u no valor de saturação respetivo.


Bloco Offset

A variável de saída do bloco PID tem de ser manipulada de modo que o DWR seja capaz de fazer ajustes de trajetórias, garantindo sempre a não saturação da variável de comando. Assim sendo, um modo de assegurar estes dois objetivos, é fazer uma média ponderada com os valores de saída do bloco PID e offset. A Equação permite calcular a variável de comando do atuador direito e a Equação permite calcular a variável de comando do atuador esquerdo. (trocar por isto)

Tendo em conta que, para um valor da variável de comando baixo, os motores estão parados, torna-se necessária a soma de um offset a esta variável, de forma que, quando o erro for nulo, ou seja, quando u=0 , a variável de comando não seja nula. Por exemplo, para um valor de offset igual a 0,7 e u=u_(sata) , a variável de comando V_(comandoR) será igual a 0,7+0,3 u_(sata) e a variável de comando V_(comandoL) será igual a 0,7-0,3 u_(sata) . Desta forma, garante-se que a variável de comando nunca será nula.

| V_(comandoR) =offset+(1-offset) u | (2.4)
| V_(comandoL) =offset-(1-offset) u | (2.4)

~~Na Figura~~~~, mostra-se a máquina de estados desenvolvida, sendo composta por quatro~~ ~~estados~~ ~~principais: S_STOPPED, S_RECEIVE, MOVEMENT e S_ERROR. No primeiro, o DWR está parado à espera de algum estímulo. O segundo dedica-se à comunicação de novas rotas entre a unidade de controlo e o robô. O terceiro está relacionado com todo o tipo de operações que o DWR terá de efetuar durante o tempo em que se encontra em movimento. O quarto é um estado crítico e o DWR apenas deve transitar para este caso ocorra algum erro que comprometa o normal funcionamento do sistema.~~

~~O estado de MOVEMENT pode ser subdividido em quatro estados secundários: S_FLW_LINE, S_RD_RFID, S_NEXT_MOV e S_ROTATE. O primeiro implementa um algoritmo responsável pelo seguimento de linha. O segundo é responsável pela leitura de um cartão RFID de identificação unívoca para cada cruzamento. O terceiro é um estado de decisão responsável por encaminhar o sistema para um estado que esteja de acordo com as entradas dos sensores e com o percurso a realizar. O quarto executa o controlo da mudança de direção num cruzamento.~~

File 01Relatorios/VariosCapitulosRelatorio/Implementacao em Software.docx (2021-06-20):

Implementação em Software - 1.1 Descrição de Software e Módulos Criados

Na criação de software torna-se indispensável a utilização de métodos de programação modular que consistem na divisão do código em diversos ficheiros, denominados de módulos. Esta abordagem permite estruturar um programa de forma mais clara, agrupando funções e variáveis relacionadas num mesmo ficheiro. Além disso, facilita a reutilização de funções e a manutenção de código.

A fig x representa a divisão do software criado nos vários módulos e as suas interações, em que, FSM significa Finite State Machine (Máquina de estados) e HAL significa Hardware Abstraction Layer. De notar que, tal como apresentado na legenda na figura, os módulos estão agrupados por cores e as setas são usadas para representar as interações entre os módulos indicando a relação de dependência. Por exemplo, o módulo FSM depende do módulo Motion, mas Motion não depende do módulo FSM, em que Motion pertence ao grupo de módulos que controlam o movimento (Movement Modules).


Legenda: Divisão do software criado nos vários módulos.

Começando pela descrição dos módulos que controlam o movimento (representados a cor avermelhada, na figura x), na camada de interação com o hardware existem três módulos: Motor, QTR e Stop Sensors. O módulo Motor, permite o controlo de um motor através de um timer com canal PWM, que efetua a variação da tensão de alimentação média do motor, por modulação de largura de impulso (PWM). O sentido de rotação do motor é definido por dois pinos GPIO, IN1 e IN2, tal como apresentado na tabela y (tabela do driver) do capítulo anterior. Na fig x (fig abaixo struct) é apresentada a estrutura que define um motor.


Legenda: Estrutura que define um motor.

O módulo QTR inicializa o array de sensores do seguidor de linha [ref], possibilitando a obtenção do valor analógico e do valor lógico de cada um dos sensores, sendo o valor lógico alto definido a partir de 2,45 V. A leitura dos valores dos sensores do QTR é feita através do DMA. Na fig x, encontram-se representados, em forma de um enumerado, todos os sensores do array de sensores usados.


Legenda: Enumerado que representa os sensores do QTR utilizados.

O módulo Stop Sensors permite detetar as marcas de paragem (cruzes) e eventuais obstáculos que apareçam no percurso do DWR. Este módulo utiliza dois sensores do módulo QTR para fazer a deteção das marcas de paragem, SENSOR1 e SENSOR8, e um sensor de obstáculos. Tal como no módulo QTR, a leitura dos valores do sensor de obstáculos é feita através do DMA. Definiu-se que o sensor de obstáculos sinaliza a presença de um objeto na trajetória do robô quando este se encontra a, aproximadamente, 15 cm de distância, correspondendo a um valor digital de 0x2000. Este módulo tem dois códigos de erro associados: E_ST_CROSS_FOUND, usado quando deteta uma marca de paragem, e E_ST_OBS_FOUND, usado quando deteta um obstáculo.

O módulo Move controla o movimento dos motores, definindo as suas velocidades e sentidos de rotação. Além disso, este módulo inicializa os dois motores a serem usados: motor direito e motor esquerdo.

O módulo PID implementa o algoritmo do controlador PID, tal como apresentado no cap x. Na fig x, é apresentada a estrutura que define as variáveis utilizadas para realizar o algoritmo PID.


Legenda: Estrutura que agrupa as variáveis de cálculo do algoritmo PID.

O módulo Timeout permite gerar quatro timeouts, com duração em segundos, como apresentado na fig x. Quando um timeout termina, a flag respetiva será ativa de forma a sinalizar o sucedido. Para isso, este módulo utiliza um timer que gera uma interrupção a cada 1 segundo.

Legenda: Duração dos vários timeouts, em segundos, e definição das flags respetivas.

O módulo Lfollower implementa o seguidor de linha, através dos sensores do QTR já mencionados, aplicando o algoritmo PID, utilizando o módulo Move para provocar uma alteração na velocidade de rotação dos motores. Além disso, este módulo implementa uma função que permite rodar o robô numa direção, direita ou esquerda, até que o sensor do QTR no lado correspondente à direção de rotação, SENSOR1 e SENSOR8, respetivamente, detetem novamente a linha. Caso nenhum sensor detete a linha durante o movimento de rotação, este será parado ao fim de um timeout predefinido, ROTATE_TIMEOUT apresentado na fig x. Este módulo tem dois códigos de erro associados: E_LF_OFF, usado quando se tenta utilizar o seguidor de linha antes de o inicializar, e E_LF_NO_LINE, usado quando o seguidor de linha não encontra uma linha para seguir. Quando ROTATE_TIMEOUT termina, é utilizado o código de erro E_TIMEOUT.

O módulo Motion controla o movimento do robô utilizando o seguidor de linha, os sensores de paragem e o sensor de obstáculos. Na fig x, está representado um enumerado com os possíveis estados de movimento. Sempre que algum dos erros apresentados anteriormente acontece, é efetuada a mudança do estado do movimento para o estado respetivo.


Legenda: Enumerado com os possíveis estados de movimento.

Este módulo utiliza um timer para provocar uma interrupção a cada 10 milissegundos, de forma a aplicar o seguidor de linha e verificar os sensores de paragem. Quando um obstáculo é detetado, o estado do movimento passa a ser MOT_HOLD, iniciando-se a contagem de um timeout com duração HOLD_TIMEOUT, tal como apresentado na fig x. Quando este timeout acaba, o estado do movimento passa para MOT_TIMEOUT. Quando não é detetada nenhuma linha durante o movimento, o estado do movimento passa para MOT_ERR.

O módulo RFID permite ler um cartão RFID, obtendo-se um CardID, a sua representação em string e o seu tipo, tal como apresentado na fig x. O enumerado da fig x representa o estado do leitor RFID. Quando a leitura é bem-sucedida, o seu estado será MI_OK. Se houver um erro na leitura ou passar demasiado tempo após o início da leitura, o estado do leitor RFID será MI_ERR ou MI_TIMEOUT, respetivamente.

(a) | (b)

Legenda: Módulo RFID: a) Estrutura que define um cartão RFID; b) Estado do leitor RFID.

Relativamente aos módulos da comunicação, o módulo Bluetooth é responsável por receber e executar uma trama via UART, que está conectada a um dispositivo Bluetooth. Na fig x, está representado, em enumerado, o estado do módulo Bluetooth. Quando uma trama for recebida com sucesso o estado será BLUET_OK. Se uma trama estiver a ser recebida, o estado será BLUET_RECEIVING, enquanto quando o estiver pronto para receber, o estado será BLUET_READY.

Legenda: Estado do módulo Bluetooth.

O módulo Commands define a lista de comandos válidos para esta aplicação. Na fig x está representada a estrutura que define um comando, sendo composta pela string que define o comando, uma string com um texto de ajuda para o comando e a função que o executa (callback).

Legenda: Definição de um callback de um comando e da estrutura que define um comando.

O módulo Parser permite analisar uma trama, dividindo-a em diferentes strings a partir de um delimitador. Além disso, se a trama for um comando válido, este módulo executa a função relativa a este comando. O módulo Cmd Parser permite interpretar um comando, definido no módulo Commands, através do módulo Parser, e executá-lo.

O módulo Route permite criar uma rota com vários pontos de paragem (checkpoints). Assim, na fig x, está representada a estrutura que define um ponto de paragem numa rota, contendo uma string com o identificador do checkpoint (RFID) e a ação a executar nesse ponto de paragem (action).

Legenda: Ações possíveis a realizar num checkpoint, e, definição de um checkpoint.

O módulo Debounce efetua o debounce de um botão de pressão associado a um pino GPIO, por software, através de um algoritmo janela deslizante, tal como mostra a figura x.

Legenda: Definição de uma janela deslizante.

Uma janela deslizante é um algoritmo que permite armazenar um conjunto de valores, neste caso, um conjunto de bits numa janela de 8 bits (window), e também, saber quantos bits a nível lógico alto existem na janela. Como definido na estrutura apresentada na fig x, o módulo Debounce utiliza uma janela deslizante (sw) para que, quando o número de bits a nível lógico alto for superior a um certo valor, menor do que o tamanho da janela, coloque o pin_output, que representa o sinal resultante da aplicação do debounce ao pino GPIO, a nível lógico alto. Para isso, este módulo utiliza um timer que gera uma interrupção a cada 50 milissegundos.


Legenda: Definição da estrutura debounce.

O módulo FSM implementa a máquina de estados, descrita no capítulo z, que controla a evolução do estado de funcionamento do robô. O enumerado ilustrado na fig x apresenta os possíveis estados de funcionamento do DWR.


Legenda: Estados da máquina de estados.

Os estados são executados de forma contínua, até que um estímulo específico faça a máquina de estados transitar para outro estado. Para isso, criou-se um array de funções, fsm_func_ptr, com as funções que implementam os diferentes estados da máquina de estados, tal como mostra a fig x a). Este array de funções é acedido com base no valor do estado atual, state. Após a execução do estado, o valor do próximo estado, nstate, é atribuído ao estado atual, como apresentado na fig x b).


a) | b)

Legenda: Definição da máquina de estados: a) Array de funções de estado;

b) Execução da máquina de estados.

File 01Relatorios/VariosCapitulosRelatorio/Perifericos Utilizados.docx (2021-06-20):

Periféricos Utilizados

1. DMA

Uma unidade de Acesso à Memória Direta (DMA) é um elemento lógico digital que pode ser usado em conjunto com o microprocessador para executar as operações de transferência de memória. Deste modo reduz-se, significativamente, a carga da unidade central de processamento (CPU). Os dispositivos compartilham o barramento de memória e os barramentos de periféricos com o processador (CPU), tal como mostrado na Figura.


Exemplo de transferência do DMA

No diagrama, o dispositivo DMA lê o valor de um periférico a partir do barramento do periférico e grava na memória através do barramento de memória. Na STM o princípio é o mesmo, mas com os vários barramentos de periféricos.

Na STM32F767ZI existem dois controladores DMA (DMA1 e DMA2) que possuem dezasseis streams (canais de acesso à memória) no total, oito para cada. Cada stream pode ter até dezasseis canais de requisição independentes, configuráveis, como apresentado na figura.


(a)


(b)

Mapa de pedido de DMA

A priorização da stream pode ser definida pelo utilizador em quatro níveis: baixa, média, alta e muito alta. Além disso, cada stream pode ser configurada com um tamanho específico de oito, dezasseis ou trinta e dois bits. Na figura, pode constatar-se que as transferências permitidas são entre memórias, entre o periférico e a memória e entre a memória e o periférico. É de notar que apenas o controlador do DMA 2 está habilitado a executar transferências entre memórias.


Endereços da fonte e do destino

O DMA pode ser configurado em dois modos de transferência de dados: modo direto, em que a transferência de dados é feita de forma imediata, ou modo first in first out (FIFO), em que os dados são armazenados temporariamente antes de serem transmitidos para a memória, sendo possível selecionar entre 25%, 50%, 75% ou 100% da capacidade total da FIFO. Em relação aos tamanhos dos dados, estes podem variar entre um byte, half word (2 bytes consecutivos) ou word (4 bytes consecutivos). Outras potencialidades do DMA surgem no facto de os apontadores se auto incrementarem, possibilitando a escrita de várias posições de memória consecutivas e a reprogramação ser automática, ou seja, poder usar o modo circular. De forma a inicializar o DMA entre um periférico específico e uma memória, é necessário configurar o canal apropriadamente e definir todas as configurações necessárias de acordo com a figura.


Configurações possíveis do DMA

2. ADC

Um Analog to Digital Converter (ADC) converte sinais analógicos em sinais digitais, permitindo aos microcontroladores comunicar com o mundo real. Deste modo, o processador consegue fazer cálculos e tomar decisões com base nos valores amostrados. A STM32F767ZI possui três ADCs de aproximação sucessiva, com dezasseis canais cada, e uma resolução, configurável, de doze, dez, oito ou seis bits. Um conversor por aproximação sucessiva (Figura) possui um comparador e um Digital to Analog Converter (DAC) interno para aproximar, sucessivamente, o valor de saída do ADC ao valor de entrada.


O ADC pode ser configurado em Single-channel ou Multichannel (scan mode). No primeiro, apenas é lido um canal, ao passo que, no segundo, são lidos vários canais sucessivamente. Além disso, pode ser configurado em single conversion mode e continuous conversion mode. No primeiro, o ADC realiza uma única conversão e armazena o resultado no registo de dados (DR). No segundo, o ADC inicializa uma nova conversão logo que a conversão em curso termine. As possíveis configurações destes modos de operação estão apresentadas na Figura.


(a) | (b) | (c) | (d)

Modo de funcionamento independente (a) Single-channel, single conversion mode; (b) Multichannel, single conversion mode; (c) Single-channel, continuous conversion mode; (d) Multichannel, continuous conversion mode

O ADC possui um único registo de dados, por isso, quando se lê múltiplas entradas analógicas, é essencial que os dados sejam lidos entre duas amostras. Isto pode ser realizado através de polling, interrupção ou DMA. Interrupções e DMA podem ser disparados no final de cada conversão. Quanto à gama de valores de entrada do ADC, este nunca não suporta valores de tensão negativas nem superiores a 3,3 V.

Outros modos de operação -> Dizer que não se vai especificar

3. TIMER

Um timer é um dispositivo de hardware capaz de medir uma base de tempo. Pode ser usado, por exemplo, para ativar eventos a frequências ou atrasos conhecidos, gerar sinais a várias frequências, sinais de saída modulados por largura de pulso (PWM) e medir pulsos de entrada.

A STM32F767ZI tem dois timers básicos (TIM6 e TIM7), oito timers do tipo general-purpose (TIM2, TIM3, TIM4, TIM5, TIM9, TIM10, TIM11, TIM12, TIM13 e TIM14) e dois timers do tipo advanced-control (TIM1 e TIM8). Os timers básicos são os mais simples. Consistem em contadores, com contagem crescente, de 16-bits com auto-reload controlados por um prescaler programável. Podem ser usados como timers genéricos para gerar bases de tempo, circuitos de sincronização para despoletar digital to analog converters (DAC) e gerar interrupções/DMA através de update events. Os General purpose estão divididos em vários grupos. Um dos grupos é composto pelos timers TIM2, TIM3, TIM4 e TIM5. Consistem em contadores, de contagem crescente, decrescente e crescente/decrescente, de 16-bits (TIM3 e TIM4) ou 32-bits (TIM2 e TIM5) com auto-reload controlados por um prescaler programável. Cada um destes timers possui quatro canais independentes que podem ser configurados como output compare, one-pulse mode output, input capture e PWM generation. Podem ser usados para gerar interrupções/DMA através de update events, trigger events, input capture events e output compare events. Outro grupo é constituído pelos timers TIM9 e TIM12. Consistem em contadores, de contagem crescente, de 16-bits com auto-reload controlados por um prescaler programável. Cada um destes timers possui dois canais independentes que podem ser configurados como output compare, one-pulse mode output, input capture e PWM generation. Podem ser usados para gerar interrupções através de update events, trigger events, input capture events e output compare events. O último grupo é constituído pelos timers TIM10, TIM11, TIM13 e TIM14. Consistem em contadores, de contagem crescente, de 16-bits com auto-reload controlados por um prescaler programável. Cada um destes timers possui um único canal independente que pode ser configurado como output compare, one-pulse mode output, input capture e PWM generation. Podem ser usados para gerar interrupções através de update events, input capture events e output compare events. Estas informações podem ser observadas de forma mais compacta na figura


Todos os timers estão mapeados em barramentos do mapa de memória. Na tabela pode-se ver os barramentos a que cada timer pertence, bem a frequência máxima do barramento.

Mapeamento dos Timers

Timer | 1 | 2 | 3 | 4 | 5 | 6 | 7 | 8 | 9 | 10 | 11 | 12 | 13 | 14
APB1(108 MHz) | | x | x | x | x | x | x | | | | | x | x | x
APB2(216 MHz) | x | | | | | | | x | x | x | x

Para configurar o timer com a frequência desejada é necessário configurar os valores de prescaler de preload. O prescaler divide a frequência de oscilação do barramento, ao passo que o preload define o número de contagens do timer. Por exemplo, se o barramento tiver uma frequência de 108 MHz e o prescaler um valor de 108 – 1 (a contagem do registo começa em zero), a frequência do timer será de 108 MHz / 108 = 1 MHz, o que equivale a uma base de tempo de 1 us. Se o valor de preload for 10 – 1, o timer terá uma frequência de 1 MHz / 10= 100 KHz, ou seja, um período de 1 / 100 KHz =10 us. Tendo em conta estes parâmetros e o valor da frequência do barramento do timer em questão (figura), é possível calcular a frequência do timer usando a Equação.

| UpdateEvent= (Timer_(clock))/((Prescaler+1)(Period+1)) | (2.4)

4. UART

A universal asynchronous receiver transmitter (UART) é uma comunicação série largamente usada para comunicar entre dois dispositivos, como sistemas embebidos, microcontroladores e computadores. Na comunicação UART, a comunicação direta entre dois dispositivos faz-se através de duas linhas de dados como representado na figura.

Esquema de ligação entre 2 UARTs

Este periférico transmite dados de forma assíncrona, ou seja, não necessita de um sinal de clock para se manter sincronizado. Em vez disso, o emissor acrescenta bits ao pacote a ser transmitido sinalizando o início e o fim dos dados a ser transferidos, tal como mostrado na figura.


Estrutura de um pacote de dados enviado por UART

Quanto ao recetor, após detetar o start bit, começará a ler os bits que se seguem a uma determinada frequência, denominado baud rate. Expresso em bits por segundo (bps), este é definido como sendo uma medida de velocidade de transmissão. Ambas as UART têm de operar ao mesmo baud rate para não ocorrer erros na transmissão, antes da inicialização da comunicação, ambas as UARTs têm de ser configuradas com o mesmo baud rate e com a mesma estrutura de pacotes.

Na STM32F767ZI encontram-se disponíveis 8 módulos UART do quais 4 (USART1, USART2, USART3 e USART6) podem ser configurados em modo síncrono. A figura mostra as funcionalidades que cada UART, presente na placa, possui.


Figura de funcionalidades existentes para cada UART

Cada UART pode ser configurada para comunicação assíncrona ou síncrona (no caso das UARTs previamente referidas), pode ser ainda configurada em full-duplex ou half-duplex, com baud-rate até 27 Mbits/s (quando clock source da UART é o clock do sistema) ou com deteção automática do baud rate. A estrutura dos pacotes de dados é modificável, podendo escolher ter 7,8 ou 9 bits de dados, 1 ou 2 stop bits e uma definição da ordem da transmissão de dados com MSB-first (bit mais significativo primeiro) ou LSB-first (bit menos significativo primeiro). Para além disso, existem mais 14 interrupt flags para controlo de fluxo de dados e erros. Possui, ainda, a possibilidade de funcionar com o DMA para comunicação continua e para buffers de dados recebidos e transmitidos, com o intuito de serem guardados ou adquiridos da SRAM. As UARTs podem também configuradas para a utilização do padrão de comunicação série RS-232 ou o padrão RS-485. Os principais elementos das UARTs localizadas na STM32F767ZI, ~~e~~ bem como as suas interações encontram-se descritas na figura.


Diagrama de blocos da USARTs

5. SPI

A Serial Peripheral Interface (SPI) é um protocolo de comunicação de curto alcance criado para a troca de dados entre microcontroladores ou entre microcontroladores e sensores. O SPI é síncrono e necessita que o transmissor e o recetor estejam sincronizados através de uma linha de clock partilhada. Este suporta transferências de dados em três modos: full-duplex (2 linhas de dados), half-duplex (1 linha de dados bidirecional) ou simplex (1 linhas unidirecional).

Os dispositivos conectados por SPI encontram-se numa relação master-slave. O master é, tipicamente, um microcontrolador que envia instruções ao slave. Este, em vários casos, trata-se de um sensor, um chip de memória ou um display.

De modo a proceder à comunicação full-duplex entre um dispositivo master e um dispositivo slave, estes devem ser conectados segundo a configuração apresentada na figura.


Esquema de ligação entre Master e Slave.

O protocolo SPI especifica 4 linhas lógicas para a transferência de dados:

- SCLK: Serial Clock, uma saída proveniente do master para sincronizar as transferências de dados nas linhas MISO e MOSI;
- MOSI: Master Out Slave In, Saída de dados do master com destino ao slave;
- MISO: Master In Slave Out, Saída de dados do slave com destino ao master;
- SS: Slave Select, através desta linha o master pode selecionar com qual dispositivo pretende comunicar.

A STM32F767ZI possui 6 interfaces SPI que suportam comunicação full-duplex, half-duplex e simplex, permitindo enviar blocos de dados de 4 a 16 bits. Além disso, o clock e a ordem dos dados é configurável por software, existem interrupt flags dedicadas à transmissão e receção de dados e cada interface possui 2 FIFOs de 32 bits (uma para receção e outra para a transmissão) com capacidade de uso conjunto com o DMA. Os principais elementos da interface SPI localizada na STM32F767ZI e as suas interações encontram-se descritas na figura.


Diagrama de blocos das interfaces SPI

Tabela Periféricos

Configuração ADC2 (com base no stm32cube)
Mode | | Independent Mode
Clock Prescaler | | PCLK2 divide by 4
Resolution | | 12-bits
Data Alignment | | Right alignment
Scan Conversion Mode | | Enable
Conversion Mode | | Continuous
DMA Continuous Requests | | Enable
End Of Conversion Selection | | EOC flag at the end of single channel conversion
Number Of Conversion | | 1
External Trigger Conversion Source | | Regular conversion
Rank 1 | Channel | 1
| Sample Time | 3 Cycles
Global Interrupt | | Enable

Configuração ADC2 (com base no stm32cube)
Mode | | Independent Mode
Clock Prescaler | | PCLK2 divide by 4
Resolution | | 12-bits
Data Alignment | | Right alignment
Scan Conversion Mode | | Enable
Conversion Mode | | Continuous
DMA Continuous Requests | | Enable
End Of Conversion Selection | | EOC flag at the end of single channel conversion
Number Of Conversion | | 6
External Trigger Conversion Source | | Regular conversion
Rank 1 | Channel | 10
| Sample Time | 3 Cycles
Rank 2 | Channel | 13
| Sample Time | 3 Cycles
Rank 3 | Channel | 9
| Sample Time | 3 Cycles
Rank 4 | Channel | 15
| Sample Time | 3 Cycles
Rank 5 | Channel | 8
| Sample Time | 3 Cycles
Rank 6 | Channel | 6
| Sample Time | 3 Cycles
Global Interrupt | | Enable

Configuração DMA2 (com base no stm32cube)
ADC3 | Stream | 1
| Direction | Peripheral to memory
| Priority | Low
| Mode | Circular
| Increment Address | Memory
| Data Witdth | Word
ADC2 | Stream | 2
| Direction | Peripheral to memory
| Priority | Low
| Mode | Circular
| Increment Address | Memory
| Data Witdth | Word

Em relação aos timers, foram usados quatro para aplicações distintas. Sempre que o robô deteta uma linha terminal, significa que, pouco tempo depois, terá de ler o RFID do quarto ou cruzamento correspondente. Sendo assim, é necessário um temporizador que permite encaminhar o robô para o estado de erro caso se ultrapasse o tempo estabelecido e o cartão RFID não seja lido. O tempo estabelecido foi de 1 segundo. A tabela apresenta as configurações usadas para que este periférico funcionasse como desejado.

Configuração TIM3 (com base no stm32cube)

Counter Settings
Prescaler | 60000 - 1
Counter Mode | Up
Counter Period | 1800 - 1
Internal clock divison | No division
Auto-reload preload | Enable

Trigger Output
Master/Slave Mode | Disable
Trigger Event Selection | Update Event

NVIC
Global Interrupt | Enable

O controlo dos motores afeta, diretamente, a tensão de alimentação do motor, ou seja, com um sinal de PWM. Sendo assim, foi necessário utilizar um timer, TIM4 no caso, que possibilitasse a geração destes. Para o efeito, selecionou-se dois canais (3 e 4) e configurou-se em PWM Generation.

Configuração TIM4 (com base no stm32cube)

Counter Settings
Prescaler | | 108 - 1
Counter Mode | | Up
Counter Period | | 100 - 1
Internal clock divison | | No division
Auto-reload preload | | Enable

Trigger Output
Master/Slave Mode | | Disable
Trigger Event Selection | | Reset
Channel 3 | Mode | 1
| Pulse | 0
| Output compare preload | Enable
| Fast mode | Diasble
| CH Polarity | High
Channel 4 | Mode | 1
| Pulse | 0
| Output compare preload | Enable
| Fast mode | Diasble
| CH Polarity | High

NVIC
Global Interrupt | | Enable

Para uma implementação, de um controlador PID, em microcontrolador é necessária uma versão digital do mesmo. Com isto, recorre-se a um timer, neste caso o mais básico – TIM6, para definir a frequência de amostragem dos valores lidos pelos sensores. Neste caso, optou-se por um período de amostragem de 10 ms.

Configuração TIM6 (com base no stm32cube)

Counter Settings
Prescaler | 10800 - 1
Counter Mode | Up
Counter Period | 100 - 1
Auto-reload preload | Enable

Trigger Output
Trigger Event Selection | Update Event

NVIC
Global Interrupt | Enable

O robô contém um botão de pressão que permite, ao utilizador, iniciar a marcha. Assim, para evitar possíveis leituras erradas efetuou-se o debounce do botão. Para este ser possível de implementar tem-se que recorrer a um timer. Neste caso usou-se o TIM13 com uma base de tempo de 50 ms.

Configuração TIM13 (com base no stm32cube)

Counter Settings
Prescaler | 10800 - 1
Counter Mode | Up
Counter Period | 500 - 1
Internal clock divison | No division
Auto-reload preload | Enable

NVIC
Global Interrupt | Enable

---------------------------------------------------------------------------------------**--------------------------------------------------------------------------------------

TIM 6 -> SAMPLE TIME
TIM 3 -> TIMEOUT

TIM 13 -> DEBOUNCE

TIM 4 -> PWM

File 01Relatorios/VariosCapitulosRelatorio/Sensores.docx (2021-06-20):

### Sensores

Um sensor é um dispositivo que responde a um estímulo do ambiente, físico ou químico, produzindo um sinal que pode ser transformado noutra grandeza física para fins de medição.

Para o DWR, foram usados sensores infravermelhos, que são muito utilizados em aplicações que envolvem leitura e deteção de proximidade. Estes usam a luz infravermelha, que é uma radiação eletromagnética, de baixa frequência, estando abaixo do espetro eletromagnético da luz visível ao olho humano. Este tipo de sensores fazem a sua leitura através da utilização de um emissor, normalmente, laser ou LED, e um recetor fotoelétrico, que contém um elemento optoelétrico, como por exemplo um fotodíodo ou um fototransístor. Este recetor fotoelétrico deteta a luz vinda do emissor e converte a intensidade da luz recebida num sinal elétrico em tensão.

Perante as características acima enumeradas, os sensores infravermelhos podem ser usados para implementar sensores de obstáculos e sensores leitores de linha.

### Sensor de obstáculos

Face à aplicação do DWR, torna-se necessário implementar um sistema de deteção de obstáculos, de forma a evitar a colisão com eventuais objetos que impeçam a sua passagem. Para isso, utilizou-se o sensor de distância infravermelho [ref] da fabricante SHARP. Este sensor permite medir distâncias a objetos entre 10 e 80 cm, tendo uma saída do tipo analógico. Assim, para esta aplicação, este sensor será usado como sensor de proximidade. Este pode ser alimentado com tensões entre 4,5 V e 5,5 V, tendo sido usada uma tensão de alimentação de 5 V.

REFS

SHARP

GP2Y0A21YK0F

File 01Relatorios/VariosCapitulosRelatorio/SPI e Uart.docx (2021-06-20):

1. UART

A universal asynchronous receiver transmitter (UART) é uma comunicação série largamente usada para comunicar entre dois dispositivos, como sistemas embebidos, microcontroladores e computadores. Na comunicação UART, a comunicação direta entre dois dispositivos faz-se através de duas linhas de dados como representado na figura.

Esquema de ligação entre 2 UARTs

Este periférico transmite dados de forma assíncrona, ou seja, não necessita de um sinal de clock para se manter sincronizado. Em vez disso, o emissor acrescenta bits ao pacote a ser transmitido sinalizando o início e o fim dos dados a ser transferidos, tal como mostrado na figura.


Estrutura de um pacote de dados enviado por UART

Quanto ao recetor, após detetar o start bit, começará a ler os bits que se seguem a uma determinada frequência, denominado baud rate. Expresso em bits por segundo (bps), este é definido como sendo uma medida de velocidade de transmissão. Ambas as UART têm de operar ao mesmo baud rate para não ocorrer erros na transmissão, antes da inicialização da comunicação, ambas as UARTs têm de ser configuradas com o mesmo baud rate e com a mesma estrutura de pacotes.

Na STM32F767ZI encontram-se disponíveis 8 módulos UART do quais 4 (USART1, USART2, USART3 e USART6) podem ser configurados em modo síncrono. A figura mostra as funcionalidades que cada UART, presente na placa, possui.


Figura de funcionalidades existentes para cada UART

Cada UART pode ser configurada para comunicação assíncrona ou síncrona (no caso das UARTs previamente referidas), pode ser ainda configurada em full-duplex ou half-duplex, com baud-rate até 27 Mbits/s (quando clock source da UART é o clock do sistema) ou com deteção automática do baud rate. A estrutura dos pacotes de dados é modificável, podendo escolher ter 7,8 ou 9 bits de dados, 1 ou 2 stop bits e uma definição da ordem da transmissão de dados com MSB-first (bit mais significativo primeiro) ou LSB-first (bit menos significativo primeiro). Para além disso, existem mais 14 interrupt flags para controlo de fluxo de dados e erros. Possui, ainda, a possibilidade de funcionar com o DMA para comunicação continua e para buffers de dados recebidos e transmitidos, com o intuito de serem guardados ou adquiridos da SRAM. As UARTs podem também configuradas para a utilização do padrão de comunicação série RS-232 ou o padrão RS-485. Os principais elementos das UARTs localizadas na STM32F767ZI, ~~e~~ bem como as suas interações encontram-se descritas na figura.


Diagrama de blocos da USARTs

O objetivo da UART neste projeto é para possibilitar a comunicação com um módulo Bluetooth HC-05 [ref?]. Ao consultar o datasheet [ref HC-05 Datasheet] deste verifica-se que o formato da comunicação série é: oito bits de dados, um stop bit e nenhum de paridade podendo ainda suportar várias frequências de comunicação. Porém, dado que o modo de operação do módulo utilizado é o mais simples entre os disponíveis (Data mode e AT Commands), este opera a um baud rate de 9600 bits/s.

Deste modo, configurou-se a USART1 para manusear pacotes com oito bits de dados sem paridade, 1 stop bit e a operar um baud rate de 9600 bits/s. De seguida, as interrupções da USART1 se encontram ativas para processar os dados assim que chegam ao destino.

2. SPI

A Serial Peripheral Interface (SPI) é um protocolo de comunicação de curto alcance criado para a troca de dados entre microcontroladores ou entre microcontroladores e sensores. O SPI é síncrono e necessita que o transmissor e o recetor estejam sincronizados através de uma linha de clock partilhada. Este suporta transferências de dados em três modos: full-duplex (2 linhas de dados), half-duplex (1 linha de dados bidirecional) ou simplex (1 linha unidirecional).

Os dispositivos conectados por SPI encontram-se numa relação master-slave. O master é, tipicamente, um microcontrolador que envia instruções ao slave. Este, em vários casos, trata-se de um sensor, um chip de memória ou um display.

De modo a proceder à comunicação full-duplex entre um dispositivo master e um dispositivo slave, estes devem ser conectados segundo a configuração apresentada na figura.


Esquema de ligação entre Master e Slave.

O protocolo SPI especifica 4 linhas lógicas para a transferência de dados:

- SCLK: Serial Clock, uma saída proveniente do master para sincronizar as transferências de dados nas linhas MISO e MOSI;
- MOSI: Master Out Slave In, Saída de dados do master com destino ao slave;
- MISO: Master In Slave Out, Saída de dados do slave com destino ao master;
- SS: Slave Select, através desta linha o master pode selecionar com qual dispositivo pretende comunicar.

A STM32F767ZI possui 6 interfaces SPI que suportam comunicação full-duplex, half-duplex e simplex, permitindo enviar blocos de dados de 4 a 16 bits. Além disso, o clock e a ordem dos dados é configurável por software, existem interrupt flags dedicadas à transmissão e receção de dados e cada interface possui 2 FIFOs de 32 bits (uma para receção e outra para a transmissão) com capacidade de uso conjunto com o DMA. Os principais elementos da interface SPI localizada na STM32F767ZI e as suas interações encontram-se descritas na figura.


Diagrama de blocos das interfaces SPI

Pelo indicado na datasheet do chip MFRC522 [ref NXP - MFRC522], este atua como slave e aguenta velocidades de transferência de dados até 10 Mbits/s. Para além disso, é mostrado que durante a receção e transmissão de dados o módulo envia o bit mais significativo primeiro (MSB) e que os dados transmitidos são estáveis durante a transição ascendente do clock e são alterados durante a transição descendente.

Como existem 6 interfaces disponíveis, optou-se por utilizar a interface SPI3, dado que os pinos que esta usa para a comunicação não entram em conflito com pinos usados por outros periféricos. Possuindo a informação necessária e consultando o datasheet do microprocessador referente ao SPI [ref – RM0410], configurou-se a interface SPI3 para funcionar com dados no formato Motorola com o tamanho de 8 bits em que o MSB é enviado primeiro. Também se configurou o clock da interface para a transferência de dados ocorrer a 3,375 Mbits/s ao colocar o prescaler a 16 (assumindo que o clock do barramento APB1 é 54 Mhz) e configurou-se a polaridade do clock (CPOL) a low e a fase deste (CPHA) a 0, de modo executar a captura dos dados provenientes do MFRC522 durante a transição ascendente.

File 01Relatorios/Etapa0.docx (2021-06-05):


Bruno Miguel Vasconcelos da Silva, a88289

Diogo Miguel Cunha Fernandes, a88262

Duarte Miguel Novo Rodrigues, a88259

Francisco Lopes Salgado, a88231

João Pedro Dias Miranda, a88237

José Tomás Lima de Abreu, a88218

DWR-19

Digital Waiter Robot

Projeto integrador

Laboratórios e Práticas Integradas II

5 março 2021

Grupo:

-Bruno Miguel Vasconcelos da Silva 88289

-Diogo Miguel Cunha Fernandes 88262

-Duarte Miguel Novo Rodrigues 88259

-Francisco Lopes Salgado 88231

-João Pedro Dias Miranda 88237

-José Tomás Lima de Abreu, 88218

Coordenador / líder:

- José Tomás Lima de Abreu, 88218

Orientador preferido:

- Luís André Magalhães de Barros

Nome do projeto:

- Digital Waiter Robot – 19 (DWR -19)

Ideia do Produto:

A ideia do produto surgiu da necessidade de atuar perante o panorama pandémico (Covid-19), mais propriamente no auxílio a pessoas que se encontrem em isolamento.

Uma pessoa em isolamento não pode ter contacto com o mundo exterior. Por este motivo, pensou-se em desenvolver um robô que faça chegar bens essenciais à pessoa em isolamento.

A função principal do produto será desempenhar o papel de um “empregado de mesa”, daí o nome “Waiter”. O termo “Digital” advém do facto de todas funcionalidades serem maioritariamente implementadas de forma digital, perfazendo o nome do robô “Digital Waiter Robot”.

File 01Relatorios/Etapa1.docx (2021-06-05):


Bruno Miguel Vasconcelos da Silva, a88289

Diogo Miguel Cunha Fernandes, a88262

Duarte Miguel Novo Rodrigues, a88259

Francisco Lopes Salgado, a88231

João Pedro Dias Miranda, a88237

José Tomás Lima de Abreu, a88218

DWR-19

Digital Waiter Robot

Projeto integrador

Laboratórios e Práticas Integradas II

Trabalho realizado sob a orientação do

Professor Luís Barros

26 março 2021

Índice

# Lista de Figuras

# Lista de Tabelas

# Acrónimos e Siglas

Acrónimo/Sigla | Significado
DWR | Digital Waiter Robot Robô Empregado de Mesa Digital
IDE | Integrated Development Environment Ambiente de Desenvolvimento Integrado
RGB | Red, Green, Blue Vermelho, Verde, Azul
RFID | Radio Frequency Identification Identificação por Rádio Frequência

# Capítulo 1 Introdução

## Introdução

Perante o atual panorama pandémico da Covid-19 [1] pretende-se, com a realização do Projeto Integrador da Unidade Curricular de Laboratórios e Práticas Integradas II (LPI II) do curso Mestrado Integrado em Engenharia Eletrónica Industrial e Computadores, a implementação de uma ideia com o objetivo de diminuir os contactos interpessoais que possam surgir no momento da entrega de bens a pessoas hospitalizadas. Esta situação pandémica é uma oportunidade para acelerar a transformação da área saúde.

Tendo em consideração que os hospitais tiveram um aumento considerável do número de internamentos [2], pretende desenvolver-se um produto que permita a entrega e recolha de bens essenciais de forma segura. De forma a facilitar a sua desinfeção e o seu manuseamento, o robô deverá ter superfícies lisas e uma interface simples.

A maioria das ideias nesta área tem como foco principal a saúde pública da população em geral, tais como, robôs de desinfeção [3], robôs que repõem o stock em hospitais [4] ou que medem a temperatura corporal através de câmaras [5]. Prevê-se que o Digital Waiter Robot (DWR) possa ser aplicado em contexto hospitalar. Na China construiu-se um robô (little peanut) [6] com a mesma finalidade, que foi utilizado num hotel para entregar comida porta a porta a hóspedes com suspeita de infeção.

A versatilidade do sistema permitirá que o DWR possa auxiliar na distribuição de bens noutros contextos dependendo das funcionalidades requeridas, como, por exemplo, na indústria hoteleira ou em ambiente doméstico.

## Enquadramento

O DWR é um robô seguidor de linha focado na automatização de um hospital. O funcionário responsável deverá fazer um pedido por cada quarto. Deverá colocar no suporte do robô o que pretende fazer chegar aos pacientes, alimentos ou medicamentos, e após submeter todos os pedidos, deverá acioná-lo e este seguirá o percurso até aos destinos. O robô fará chegar cada pedido a cada paciente, parando apenas nos quartos solicitados. Depois de atender a todos os pedidos, o DWR voltará à posição de onde partiu.

O robô terá mecanismos de proteção contra obstáculos, avisos sonoros, controlo remoto e mecanismos de deteção de segmentos do percurso.

## Especificações previstas

O DWR seguirá uma linha preta previamente colocada no piso do hospital, que define os locais acessíveis pelo robô. Como os hospitais possuem vários quartos, em vários corredores, o robô terá de ser capaz de percorrer um percurso com várias intercessões de corredores. Assim, o sistema a ser implementado será constituído por dois subsistemas: o robô DWR e a unidade de controlo. Apesar de neste projeto ser usado apenas um robô, a unidade de controlo poderá, eventualmente, controlar vários.

Como a alimentação do robô será a baterias, eventualmente, terá de ser ligado à rede elétrica para ser carregado. Assim, existirá uma estação de carregamento que estará presente num local denominado por base.

O tipo de desenvolvimento deste produto pode ser classificado como “ofensivo”. “O objetivo é colocar no mercado um produto com funcionalidades e características inovadoras ou com preço significativamente mais baixo do que produtos com funcionalidades e características equivalentes, de forma a obter para o produto quota de mercado ou aumento da quota de mercado em relação a produtos antecessores” [7].

### Especificações funcionais

A unidade de controlo será responsável por uma aplicação de interface com o funcionário e gestão de pedidos, bem como pela orientação do robô ao longo do percurso.

Cada cruzamento no percurso deverá ter um identificador único e o DWR deve ser capaz de os detetar para que possa ser corretamente orientado pela unidade de controlo. À entrada de cada quarto, deverá existir uma marca de paragem sobre a linha de percurso, como, por exemplo, uma linha perpendicular. O robô deverá detetar essas marcas e parar apenas nas marcas dos quartos indicados pela unidade de controlo. Após recolher os bens a si destinados, o paciente poderá acionar o robô de forma a que este reinicie o seguimento da linha. Assim que não existam mais pedidos pendentes, o DWR retornará à base.

Para evitar que o DWR colida, este deverá ter um sistema de deteção de obstáculos, que, ao detetar um objeto no seu percurso, fará com que o robô pare. Se ao fim de um determinado intervalo de tempo, previamente estabelecido, a via se mantiver obstruída, deverá ser emitido um sinal sonoro para alertar as pessoas ao seu redor e, além disso, uma notificação para a aplicação de interface, alertando um funcionário responsável do sucedido. Se o problema for resolvido, o DWR continuará o seu trajeto. Caso contrário, através da aplicação, pode ser estabelecida uma ligação entre o robô e um funcionário responsável, permitindo que este controle remotamente o DWR, desviando-o do obstáculo.

### Especificações técnicas

Para implementação do sistema de controlo do DWR serão usados microcontroladores STM32F767ZI-NUCLEO [8], utilizando as ferramentas STM32CubeMX [9], para configurar os seus periféricos, e Keil uVision5 [10], como IDE.

Para cumprir o objetivo de seguir de linha, usar-se-á um array de oito sensores de reflexão com saídas analógicas. Cada saída varia entre 0 V e 3,3 V, sendo proporcional à cor refletida pela superfície, apresentando uma tensão mais elevada quando a superfície for mais escura. Ao contrário dos sensores digitais que apresentam apenas dois níveis nas suas saídas, alto ou baixo, este tipo de sensores possuem uma maior sensibilidade, permitindo que o sistema de seguidor de linha apresente menos oscilações.

A deteção e identificação de intercessões de corredores será feita por meio da tecnologia RFID [11].

O sistema de deteção de obstáculos será composto por um módulo de sensores de distância infravermelhos adequado para calcular com precisão a distância a objetos que possam aparecer na frente do DWR. O sistema de alerta sonoro fará uso de um buzzer ativo.

A comunicação entre o robô e a unidade de controlo será implementada recorrendo a tecnologia Bluetooth. Além disso, esta tecnologia permitirá aos funcionários utilizar a aplicação de interface que lhes proporciona um leque de funcionalidades, tais como solicitar o transporte de bens a quartos desejados, controlar remotamente o DWR quando o percurso estiver obstruído.
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

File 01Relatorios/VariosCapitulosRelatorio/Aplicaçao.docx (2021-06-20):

# APLICAÇAO

Dado que o robô, quando em funcionamento, necessita que um funcionário realize tarefas como iniciar o robô, fazer a gestão dos pedidos para cada quarto e decidir como o mesmo deve proceder quando ocorre algum erro, decidiu-se criar uma aplicação de interface com o utilizador.

A aplicação foi criada através da ferramenta MIT App Inventor[ref], que é um software simples e útil para o desenvolvimento de aplicações para smartphones. A interface criada é de utilização simples e o seu ecrã inicial está representado na Figura X (a), no qual se é pedido para o utilizador se conectar ao robô por Bluetooth. Para isso o utilizador terá de ativar a funcionalidade Bluetooth do seu próprio dispositivo e emparelhá-lo com o dispositivo Bluetooth do DWR (referir HC
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

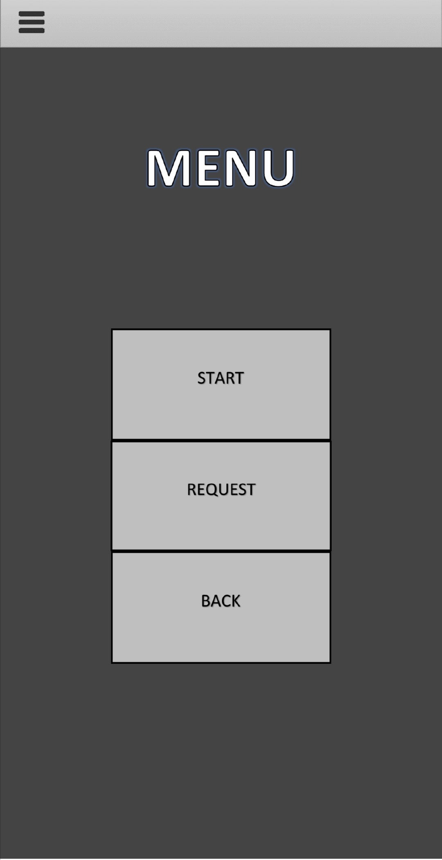
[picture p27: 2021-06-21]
01Relatorios/Images/app_menu.jpg

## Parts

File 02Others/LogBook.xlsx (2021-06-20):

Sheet: TimeTable
Day | Start Time | Tasks | End Time | Duration | Deadlines
2021-02-26 | 13:45:00 | Reunião com LBarros | 15:35:00 | 1:50:00 | Etapa0 Deadline | 2021-03-05
2021-03-03 | 14:30:00 | Entrega Etapa 0 | 14:30:00 | 0:00:00 | Etapa1 Deadline | 2021-03-26
2021-03-08 | 14:00:00 | Realização do planeamento | 16:15:00 | 2:15:00 | Etapa2 Deadline | 2021-06-22
2021-03-08 | 18:20:00 | Reunião com Nuno Cardoso | 19:30:00 | 1:10:00
2021-03-10 | 14:00:00 | Planeamento concluído. Escolha de componentes a usar. | 16:00:00 | 2:00:00 | Days to next Deadline | 2
2021-03-15 | 14:00:00 | Realização da Etapa 1 | 16:00:00 | 2:00:00
2021-03-17 | 13:15:00 | Continuação da Etapa 1 | 15:25:00 | 2:10:00 | Group Reunions
2021-03-18 | 13:10:00 | Continuação da Etapa 1 | 14:10:00 | 1:00:00 | Working Sessions | 35
2021-03-22 | 13:30:00 | Reunião com LBarros | 16:00:00 | 2:30:00 | Total (hours spent) | 187:54:00
2021-03-22 | 20:36:00 | Continuação da Etapa 1 | 23:00:00 | 2:24:00
2021-03-23 | 16:00:00 | Discussão de ideias | 16:30:00 | 0:30:00 | Members Hours Spent
2021-03-24 | 9:15:00 | Discussão de ideias | 12:00:00 | 2:45:00 | João | 227:14:00
2021-03-24 | 17:00:00 | Reunião com LBarros | 17:40:00 | 0:40:00 | Duarte | 227:14:00
2021-03-24 | 18:00:00 | Continuação da Etapa 1 | 19:30:00 | 1:30:00 | Bruno | 204:39:00
2021-03-24 | 20:45:00 | Continuação da Etapa 1 | 23:30:00 | 2:45:00 | Francisco | 204:39:00
2021-03-25 | 14:50:00 | Continuação da Etapa 1 | 15:50:00 | 1:00:00 | Diogo | 208:29:00
2021-03-26 | 17:30:00 | Entrega Etapa 1 | 17:30:00 | 0:00:00 | Tomás | 208:29:00
2021-05-03 | 13:30:00 | Discussão de ideias. Estrutura do sistema a desenvolver. | 15:10:00 | 1:40:00
2021-06-02 | 14:30:00 | Testar acionamento dos motores | 17:00:00 | 2:30:00
2021-06-02 | 21:00:00 | Testar PID | 0:00:00 | 3:00:00
2021-06-03 | 9:30:00 | Testar PID | 20:00:00 | 10:30:00
2021-06-04 | 14:30:00 | Teste Movimento Rotate | 17:00:00 | 2:30:00
2021-06-07 | 9:30:00 | Montagem Robô | 13:15:00 | 3:45:00
2021-06-07 | 14:00:00 | Montagem Robô | 23:00:00 | 9:00:00
2021-06-08 | 9:30:00 | Criação da FSM | 0:00:00 | 14:30:00
2021-06-09 | 0:00:00 | Implementação da FSM | 1:00:00 | 1:00:00
2021-06-09 | 10:00:00 | Criação da Shield para STM. Continuação da implementação da FSM | 0:00:00 | 14:00:00
2021-06-09 | 0:00:00 | Atualização dos periféricos e pinos a usar na STM | 2:00:00 | 2:00:00
2021-06-10 | 9:30:00 | Implementação e testes da FSM | 0:00:00 | 14:30:00
2021-06-11 | 9:00:00 | Implementação e testes da FSM | 18:30:00 | 9:30:00
2021-06-15 | 9:00:00 | Implementação e testes da FSM | 0:00:00 | 15:00:00
2021-06-16 | 9:30:00 | Implementação e testes da FSM | 0:00:00 | 14:30:00
2021-06-17 | 9:30:00 | Implementação e testes da FSM | 0:00:00 | 14:30:00
2021-06-18 | 9:30:00 | Implementação e testes da FSM | 0:00:00 | 14:30:00
2021-06-19 | 9:30:00 | Implementação e testes da FSM | 0:00:00 | 14:30:00
 |  |  |  | 0:00:00
 |  |  |  | 0:00:00
 |  |  |  | 0:00:00
 |  |  |  | 0:00:00

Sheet: TimeTable_Team1
Day | Start Time | Tasks | End Time | Duration | Team Stats
2021-03-31 | 14:00:00 | Estudo do seguidor de linha. Uso do DMA para ler 2 inputs do sensor | 19:20:00 | 5:20:00 | Working Sessions | 7
2021-06-01 | 9:00:00 | Implementação PID | 20:00:00 | 11:00:00 | Total (hours spent) | 39:20:00
2021-06-05 | 16:00:00 | Parte Mecânica (Furos na madeira) + Explicação PID | 19:00:00 | 3:00:00
2021-06-06 | 14:00:00 | Parte Mecânica (Acabamento dos furos na madeira + Furos aluminio + cola na entrada de carregamento) | 18:30:00 | 4:30:00 | Members
2021-06-12 | 14:00:00 | Parte Mecânica (Sensor Distancia/Sensor linha/Furos Fonte/RFID) | 18:30:00 | 4:30:00 | João
2021-06-13 | 9:00:00 | Montagem integral dos circuitos (I) | 13:00:00 | 4:00:00 | Duarte
2021-06-13 | 14:00:00 | Montagem integral dos circuitos (II) | 21:00:00 | 7:00:00
 |  |  |  | 0:00:00
 |  |  |  | 0:00:00
 |  |  |  | 0:00:00
 |  |  |  | 0:00:00
 |  |  |  | 0:00:00
 |  |  |  | 0:00:00
 |  |  |  | 0:00:00
 |  |  |  | 0:00:00
 |  |  |  | 0:00:00
 |  |  |  | 0:00:00
 |  |  |  | 0:00:00
 |  |  |  | 0:00:00
 |  |  |  | 0:00:00
 |  |  |  | 0:00:00
 |  |  |  | 0:00:00
 |  |  |  | 0:00:00

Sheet: TimeTable_Team2
Day | Start Time | Tasks | End Time | Duration | Team Stats
2021-04-02 | 20:30:00 | Estudo do modulo RFID | 21:30:00 | 1:00:00 | Working Sessions | 5
2021-04-14 | 18:30:00 | Criação do modulo para a leitura de etiquetas RFID | 23:20:00 | 4:50:00 | Total (hours spent) | 16:45:00
2021-05-05 | 13:50:00 | Continuação da implementação do modulo RFID + documentação | 17:45:00 | 3:55:00
2021-06-05 | 14:30:00 | Estudo e Implementação do Bluetooth | 18:30:00 | 4:00:00 | Members
2021-06-11 | 21:00:00 | Diagramas mecânicos | 0:00:00 | 3:00:00 | Bruno
 |  |  |  | 0:00:00 | Francisco
 |  |  |  | 0:00:00
 |  |  |  | 0:00:00
 |  |  |  | 0:00:00
 |  |  |  | 0:00:00
 |  |  |  | 0:00:00
 |  |  |  | 0:00:00
 |  |  |  | 0:00:00
 |  |  |  | 0:00:00
 |  |  |  | 0:00:00
 |  |  |  | 0:00:00
 |  |  |  | 0:00:00
 |  |  |  | 0:00:00
 |  |  |  | 0:00:00
 |  |  |  | 0:00:00
 |  |  |  | 0:00:00
 |  |  |  | 0:00:00
 |  |  |  | 0:00:00

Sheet: TimeTable_Team3
Day | Start Time | Tasks | End Time | Duration | Team Stats
2021-03-31 | 21:00:00 | Diagrama geral do sistema. Deteção de quartos e cruzamentos. | 23:40:00 | 2:40:00 | Working Sessions | 4
2021-05-05 | 13:50:00 | Implementação da deteção de obstáculos, quartos e cruzamentos. | 17:45:00 | 3:55:00 | Total (hours spent) | 20:35:00
2021-06-01 | 9:00:00 | Testes ao sensor de obstáculos. Implementação dos sistemas de deteção. | 20:00:00 | 11:00:00
2021-06-12 | 21:00:00 | Implementação da FSM | 0:00:00 | 3:00:00 | Members
 |  |  |  | 0:00:00 | Diogo
 |  |  |  | 0:00:00 | Tomás
 |  |  |  | 0:00:00
 |  |  |  | 0:00:00
 |  |  |  | 0:00:00
 |  |  |  | 0:00:00
 |  |  |  | 0:00:00
 |  |  |  | 0:00:00
 |  |  |  | 0:00:00
 |  |  |  | 0:00:00
 |  |  |  | 0:00:00
 |  |  |  | 0:00:00
 |  |  |  | 0:00:00
 |  |  |  | 0:00:00
 |  |  |  | 0:00:00
 |  |  |  | 0:00:00
 |  |  |  | 0:00:00
 |  |  |  | 0:00:00
 |  |  |  | 0:00:00

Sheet: Components
Total [€] | 97.19 €
Loja | Produto | QTD | Preço_uni | HiperLink
PTRobotics | Bluetooth Module HC-05 | 1 | 8.24 € | Bluetooth Module HC-05 (https://www.ptrobotics.com/modulos-bluetooth/4364-bluetooth-module-hc-05.html)
PTRobotics | IR Emitter and Receiver LED 5mm 940nm | 2 | 1.05 € | IR Emitter and Receiver LED 5mm 940nm (https://www.ptrobotics.com/sensores-opticos/5913-ir-emitter-and-receiver-led-5mm-940nm.html)
PTRobotics | OV7670 Camera Module | 1 | 12.18 € | OV7670 Camera Module (https://www.ptrobotics.com/cameras/3928-ov7670-camera-module.html)
PTRobotics | TCS3200 Color Sensor | 1 | 10.82 € | TCS3200 Color Sensor (https://www.ptrobotics.com/sensores-opticos/4048-tcs3200-color-sensor.html)
PTRobotics | US-015 Modulo Sensor de Distância Ultrassónico 3.3 - 5V | 1 | 4.43 € | US-015 Modulo Sensor de Distância Ultrassónico 3.3 - 5V (https://www.ptrobotics.com/sensor-ultrasom/8220-us-015-modulo-sensor-de-distancia-ultrassonico-33-5v.html)
MAUSER | Módulo Leitor RFID RC522 | 1 | 2.44 € | Módulo Leitor RFID RC522 (https://mauser.pt/catalog/product_info.php?cPath=1667_2604_2607&products_id=096-8517)
EZTronics | Sensor Sharp 2Y0A21YK | 1 | 11.50 € | Sensor Sharp 2Y0A21YK (https://www.eztronics.nl/webshop2/catalog/Sensor/Distance-Range?product_id=598)
botNroll | Ficha Shell ou KK 6 vias 2,54mm | 1 | 0.16 € | Ficha Shell ou KK 6 vias 2,54mm
botNroll | Terminais para fichas shell ou KK | 6 | 0.10 € | Terminais para fichas shell ou KK
botNroll | Cartão RFID Mifare 1k S50 compatível Tag 13,56MHz | 6 | 1.38 € | Cartão RFID Mifare 1k S50 compatível Tag 13,56MHz
botNroll | Step-Down para 5V até 8A 40W com 4 Portas USB | 1 | 9.70 € | Step-Down para 5V até 8A 40W com 4 Portas USB
botNroll | Suporte para 1 pilha 18650 c/ fios | 6 | 0.85 € | Suporte para 1 pilha 18650 c/ fios
botNroll | Interruptor de painel redondo | 1 | 1.20 € | Interruptor de painel redondo
botNroll | Botão de pressão preto redondo para painel | 1 | 0.60 € | Botão de pressão preto redondo para painel
botNroll | Carregador 3 Baterias 18650 em série - AC 100~240V DC 12,6V 1A | 1 | 8.90 € | Carregador 3 Baterias 18650 em série - AC 100~240V DC 12,6V 1A
botNroll | Cabo DC 0,2m com conector recto 5,2/2,1 (9,5mm) | 1 | 1.70 € | Cabo DC 0,2m com conector recto 5,2/2,1 (9,5mm)
AlfaElektor | Suporte Fusível Auto/F.Pla >50A | 1 | 1.22 € | Suporte Fusível Auto/F.Pla >50A (https://www.alfaelektor.pt/item.php?id=2198)
AlfaElektor | Fusivel 3A | 1 | 0.10 € | Fusivel 3A (https://www.alfaelektor.pt/item.php?id=2198)
AlfaElektor | Manga Espiral Wrapping 20-60mm | 1 | 5.50 € | Manga Espiral Wrapping 20-60mm
Guimocircuito | PCB Shield STM32F767ZI | 1 |  | PCB Shield STM32F767ZI
Mauser | Barra (2x8) fêmea 2,54 mm PCB | 1 | 0.30 € | Barra (2x8) fêmea 2,54 mm PCB
Mauser | Barra (2x10) fêmea 2,54 mm PCB | 1 | 0.40 € | Barra (2x10) fêmea 2,54 mm PCB
Mauser | Barra (2x16) fêmea 2,54 mm PCB | 1 | 0.62 € | Barra (2x16) fêmea 2,54 mm PCB
Mauser | Barra (2x17) fêmea 2,54 mm PCB | 1 | 0.69 € | Barra (2x17) fêmea 2,54 mm PCB
Mauser | Barra (2x3) fêmea 2,54 mm PCB | 2 | 0.16 € | Barra (2x3) fêmea 2,54 mm PCB
Mauser | Barra (1x6) fêmea 2,54 mm PCB | 1 | 0.09 € | Barra (1x6) fêmea 2,54 mm PCB
 |  |  |  | 0
 |  |  |  | 0
 |  |  |  | 0

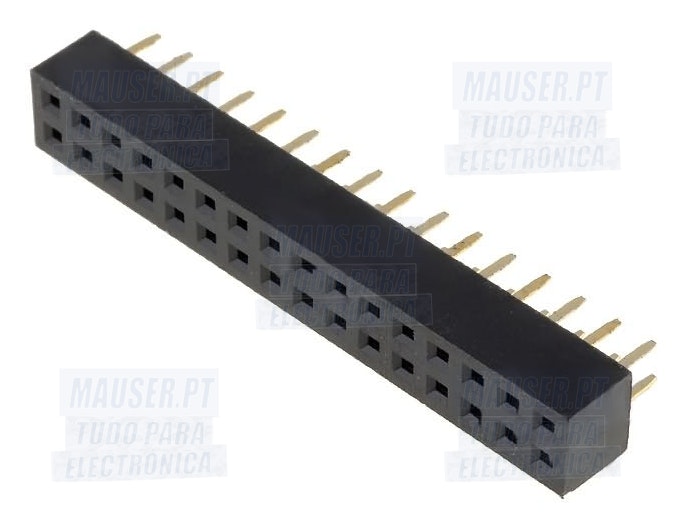
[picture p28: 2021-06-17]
01Relatorios/VariosCapitulosRelatorio/Fotos-Material/2x16.jpg

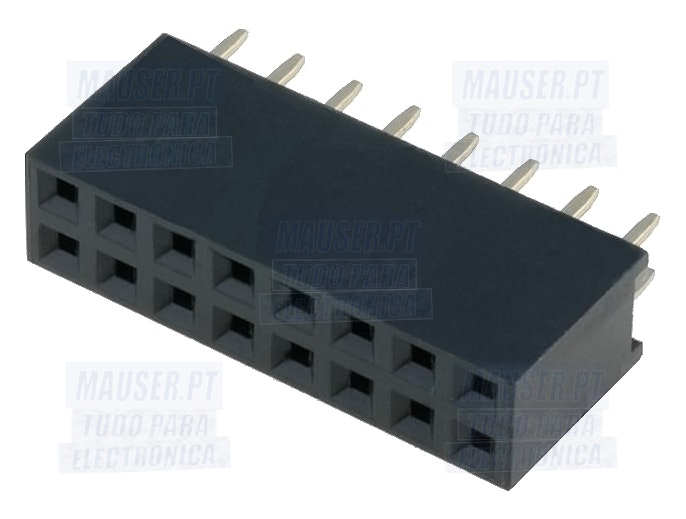
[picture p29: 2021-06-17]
01Relatorios/VariosCapitulosRelatorio/Fotos-Material/2x8.jpg

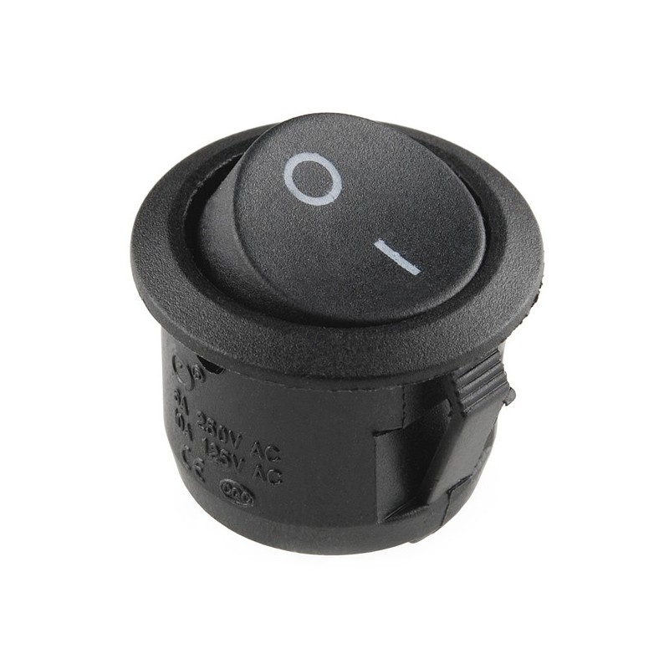
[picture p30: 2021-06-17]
01Relatorios/VariosCapitulosRelatorio/Fotos-Material/on-off.jpg

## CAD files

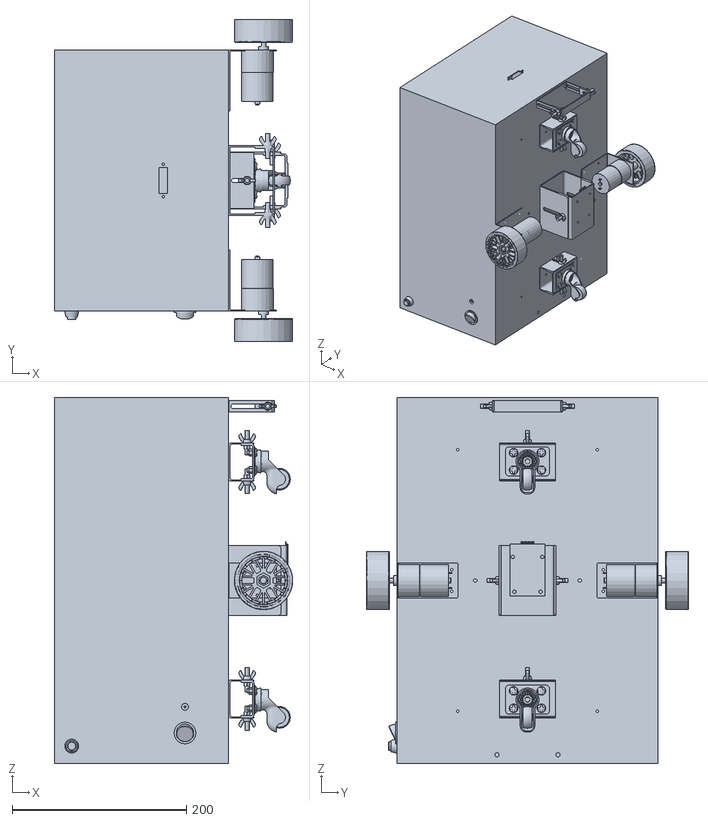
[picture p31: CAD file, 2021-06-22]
01Relatorios/Diagramas/Diagrama_Robo_v3.stl
273.6 x 370.0 x 420.0

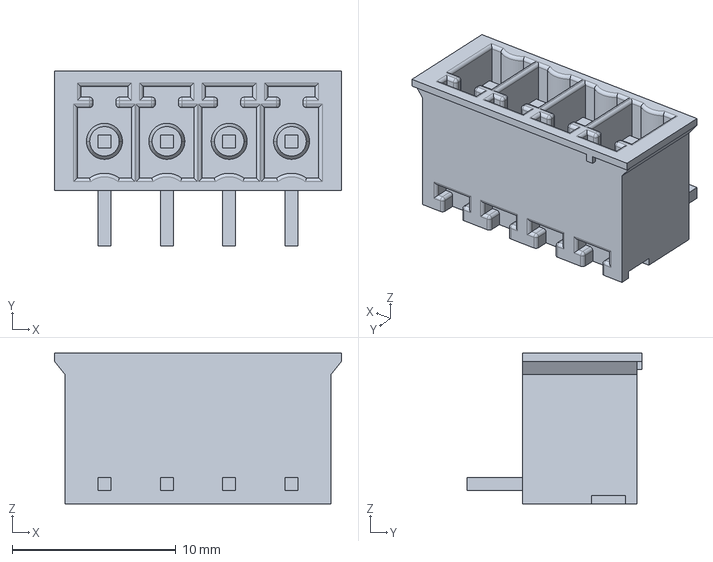
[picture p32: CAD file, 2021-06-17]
05Shield/shield_Buchanan/footprint/284513-4.step
17.5 x 10.7 x 9.20 mm

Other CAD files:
05Shield/shield_3ADCs/kicad-footprints-master/Sources/Inductor_SMD/L_Coilcraft_LPS5030.FCStd
05Shield/shield_3ADCs/kicad-footprints-master/Sources/Package_LGA/Infineon_PG-LLGA-5-1.FCStd
05Shield/shield_3ADCs/kicad-footprints-master/Sources/Package_SON/X2SON-4_1x1mm_P0.65mm.fcstd
05Shield/shield_3ADCs/kicad-footprints-master/Sources/Package_TO_SOT_THT/sod-70.fcstd
05Shield/shield_7ADCs/kicad-footprints-master/Sources/Inductor_SMD/L_Wuerth_WE-TPC-3816.FCStd
05Shield/shield_7ADCs/kicad-footprints-master/Sources/Package_LGA/Infineon_PG-LLGA-5-1.FCStd
05Shield/shield_7ADCs/kicad-footprints-master/Sources/Package_SON/X2SON-4_1x1mm_P0.65mm.fcstd
05Shield/shield_7ADCs/kicad-footprints-master/Sources/Package_TO_SOT_THT/sod-70_P5.08mm.fcstd
01Relatorios/Diagramas/LeSpeciale.dwg
05Shield/shield_3ADCs/kicad-footprints-master/Sources/Inductor_SMD/L_Wuerth_WE-TPC-3816.FCStd
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

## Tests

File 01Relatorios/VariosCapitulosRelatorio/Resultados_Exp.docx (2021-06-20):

De forma a testar as especificações acima previstas, foram realizados ensaios experimentais simulando o ambiente no qual o robô irá operar. Começou-se por testar o sensor e verificou-se que as medidas dos sensores não atingem nem 0 V nem 3,3 V.

Para verificar qual a zona de funcionamento dos motores, apurou-se qual a gama de valores de duty cycle do sinal PWM necessários para garantir a operação dos mesmos. Concluiu-se que o motor apenas possui binário de arranque suficiente quando o duty cycle do sinal PWM ronda os 65 %. Já com o motor em funcionamento, o duty cycle pode atingir um mínimo de 50 % sem que os motores parem. Estes valores permitiram ajustar o bloco de offset do controlador do módulo seguidor de linha, estabelecendo-se um valor de 70 %.

Os parâmetros do controlador PID foram obtidos através de métodos heurísticos. Verificou-se que aplicando um ganho proporcional muito superior a um, a variável de atuação do controlador aproxima-se da saturação, impedindo a realização de trajetórias curvas. Os ganhos integral e derivativo têm valores muito menores ao valor do ganho proporcional. O ganho integral é importante, principalmente, na realização de curvas mais acentuadas, uma vez que tem em conta o valor dos erros anteriores. Ao longo do tempo, a velocidade de rotação do motor que tem de fazer a compensação da trajetória aumenta e a do motor contrário reduz, quando o DWR se encontra fora da trajetória ideal. No entanto, um valor elevado no ganho integral provoca a saturação do controlador, impedindo a realização de trajetórias curvas. Definiu-se uma gama de valores válida para o ganho integrativo entre 0,2 e 0,4. O ganho derivativo também é importante na realização de curvas mais acentuadas, uma vez que faz com que o sistema responda mais cedo à variação e assim manter-se na trajetória. Estabeleceu-se o valor máximo para o ganho derivativo como 0,015, sendo que, para valores superiores a este, o DWR apresenta instabilidade no movimento, mesmo em linha reta. É de referir que se usou um período de amostragem de 10 ms.

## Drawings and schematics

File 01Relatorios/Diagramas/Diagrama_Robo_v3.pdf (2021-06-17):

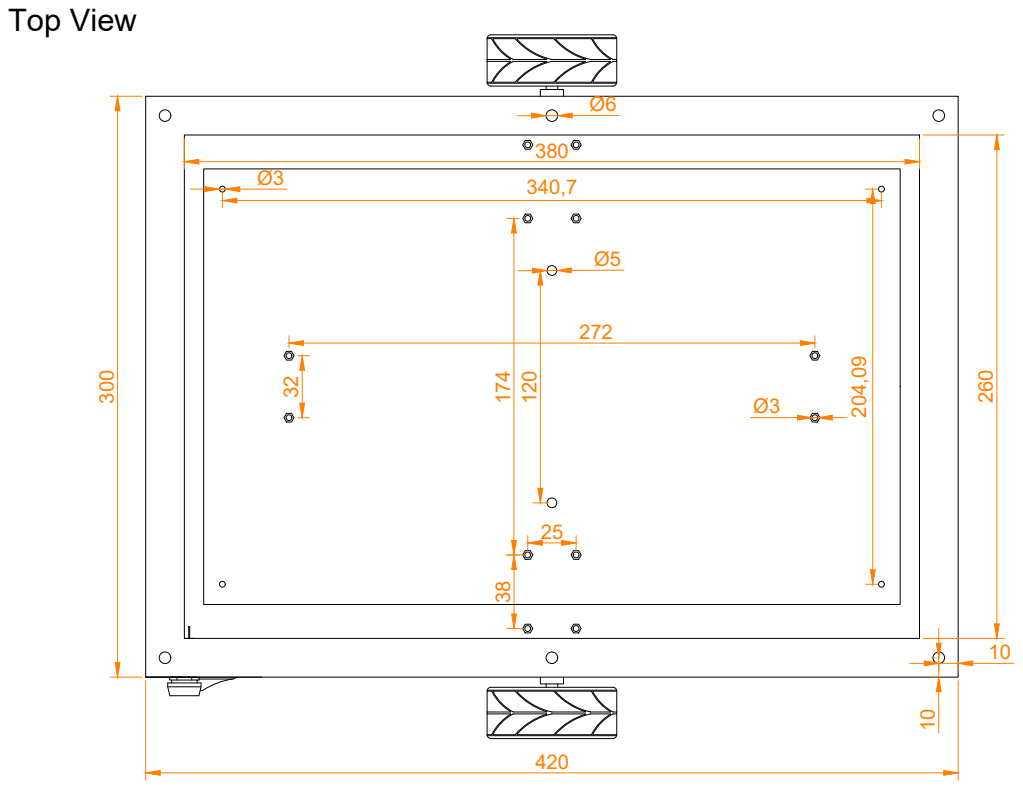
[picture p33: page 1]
260 Top View

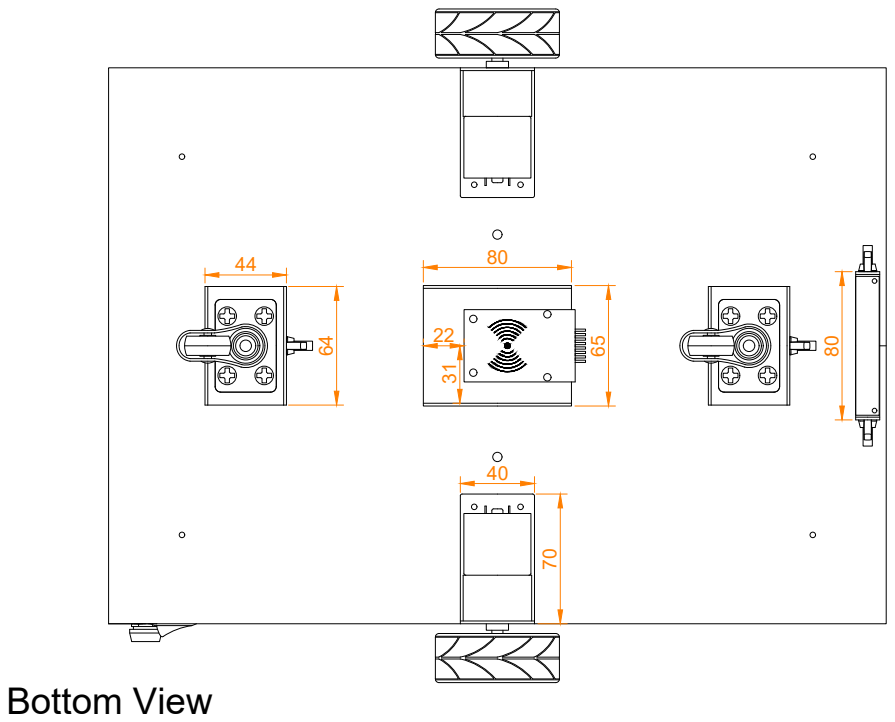
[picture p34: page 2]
Bottom View

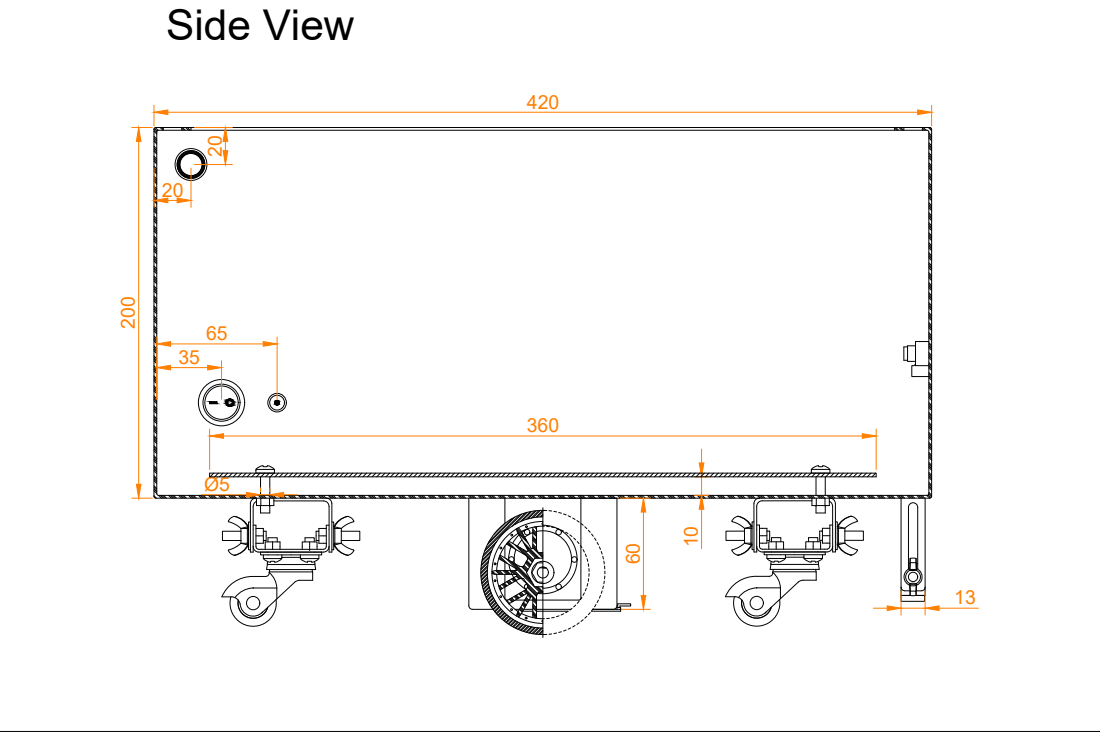
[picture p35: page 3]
Side View

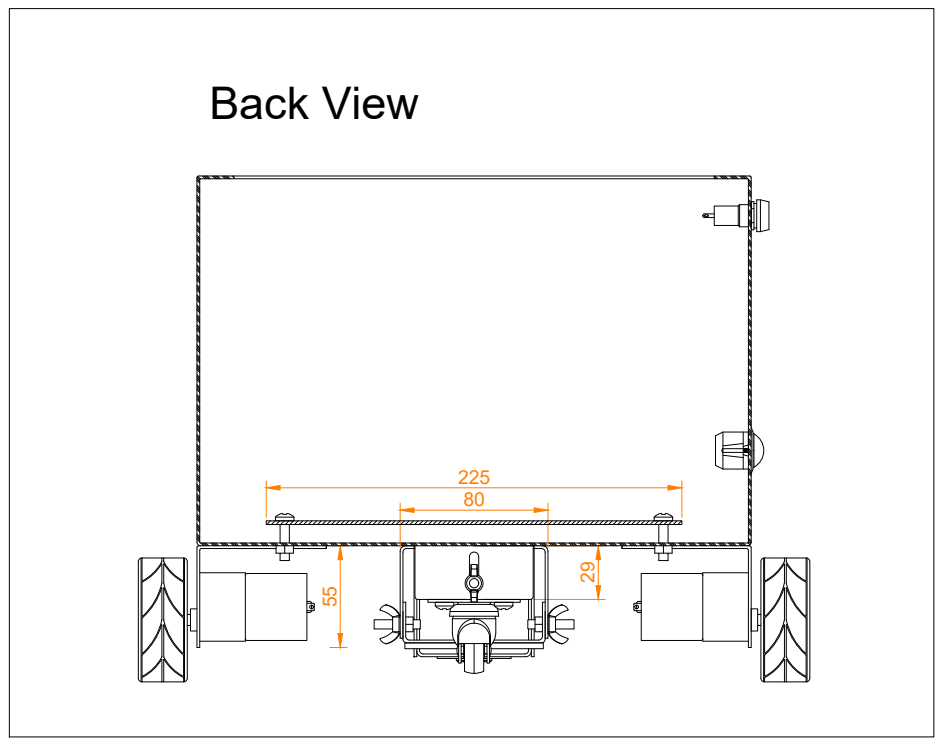
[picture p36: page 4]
Back View

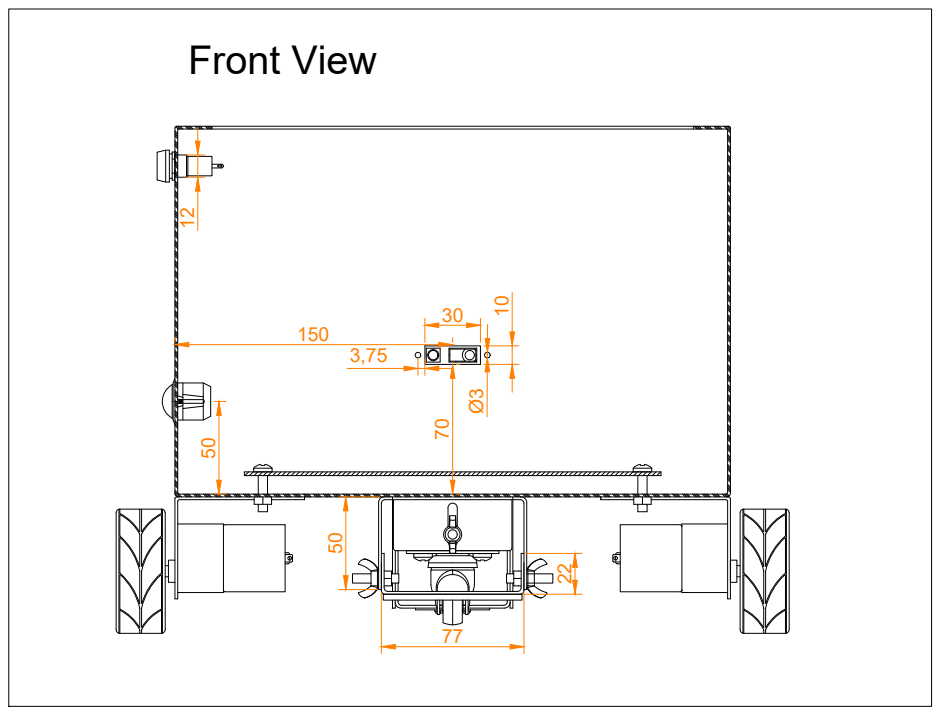
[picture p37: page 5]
Front View

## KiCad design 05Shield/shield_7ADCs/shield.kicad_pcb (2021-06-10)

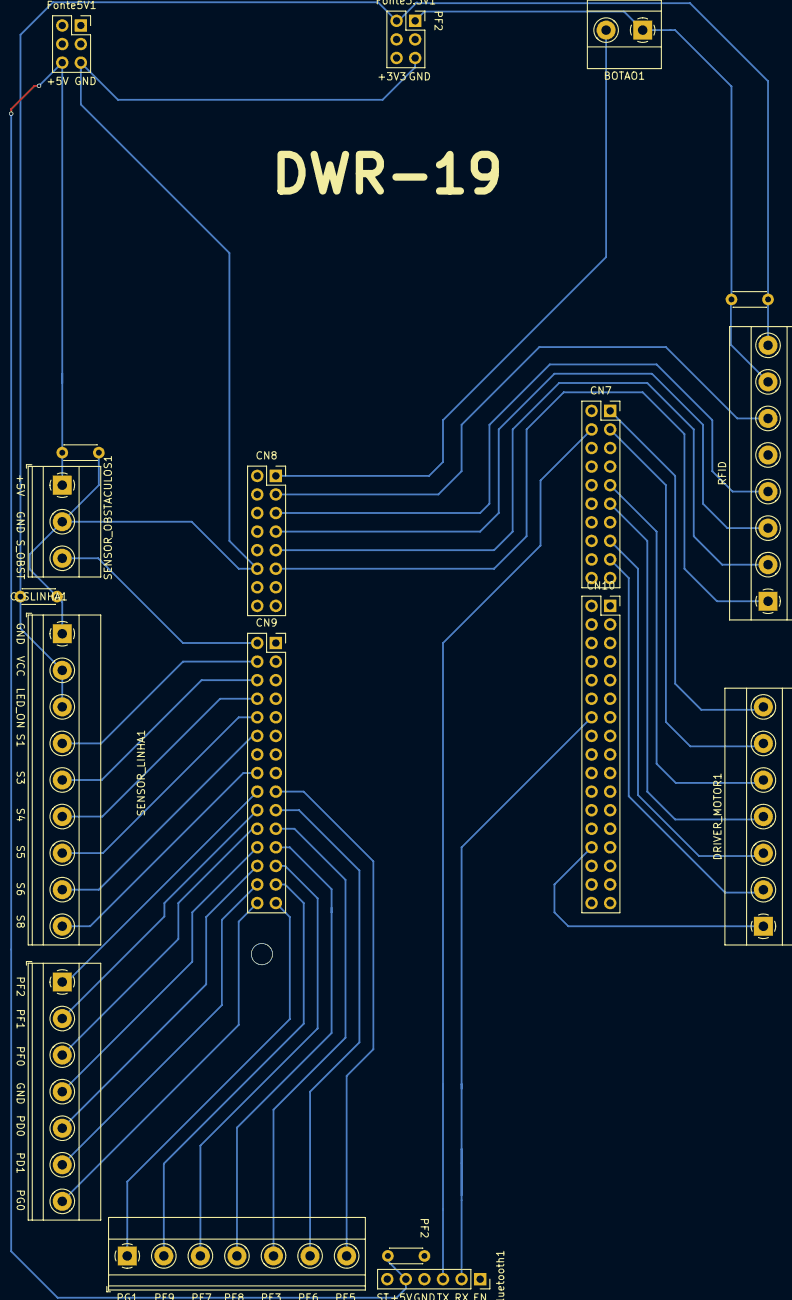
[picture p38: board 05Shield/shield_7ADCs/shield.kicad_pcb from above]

Board: 2 copper layers, 18 parts (0 on the bottom side), 40 nets.

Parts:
BOTAO1: Screw_Terminal_01x06; TerminalBlock_Phoenix_MKDS-1,5-2_1x02_P5.00mm_Horizontal
CN7: Digital; PinSocket_2x10_P2.54mm_Vertical
CN8: Digital; PinSocket_2x08_P2.54mm_Vertical
CN9: Digital; PinSocket_2x15_P2.54mm_Vertical
CN10: Digital; PinSocket_2x17_P2.54mm_Vertical
CON_LIVRE1, CON_LIVRE2: Screw_Terminal_01x07; TerminalBlock_Phoenix_MKDS-1,5-7_1x07_P5.00mm_Horizontal
C_BLUE1: C; C_Disc_D4.3mm_W1.9mm_P5.00mm
C_RFID1: C; C_Disc_D4.3mm_W1.9mm_P5.00mm
C_SLINHA1: C; C_Disc_D4.3mm_W1.9mm_P5.00mm
C_SOBST1: C; C_Disc_D4.3mm_W1.9mm_P5.00mm
DRIVER_MOTOR1: Screw_Terminal_01x07; TerminalBlock_Phoenix_MKDS-1,5-7_1x07_P5.00mm_Horizontal
Fonte3.3V1, Fonte5V1: Digital; PinSocket_2x03_P2.54mm_Vertical
RFID: Screw_Terminal_01x06; TerminalBlock_Phoenix_MKDS-1,5-8_1x08_P5.00mm_Horizontal
SENSOR_LINHA1: Screw_Terminal_01x09; TerminalBlock_Phoenix_MKDS-1,5-9_1x09_P5.00mm_Horizontal
SENSOR_OBSTACULOS1: Screw_Terminal_01x03; TerminalBlock_Phoenix_MKDS-1,5-3_1x03_P5.00mm_Horizontal
bluetooth1: Digital; PinSocket_1x06_P2.54mm_Vertical

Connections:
+3.3V: C_RFID1.1, C_SLINHA1.1, Fonte3.3V1.2, Fonte3.3V1.6, RFID.8, SENSOR_LINHA1.2, SENSOR_LINHA1.3
+5V: C_BLUE1.1, C_SOBST1.1, Fonte5V1.2, Fonte5V1.6, SENSOR_OBSTACULOS1.1, bluetooth1.5
/AVDD: CN7.5, CN10.2
/NC: CN8.2, CN9.14
/PA3: CN9.2, SENSOR_OBSTACULOS1.3
/PA5: CN7.9, DRIVER_MOTOR1.5
/PA6: CN7.11, DRIVER_MOTOR1.4
/PA7: CN7.13, CN9.16, SENSOR_LINHA1.9
/PB6: CN10.14, bluetooth1.2
/PB8: CN7.1, DRIVER_MOTOR1.7
/PB9: CN7.3, DRIVER_MOTOR1.6
/PB15: CN7.4, bluetooth1.3
/PC0: CN9.4, SENSOR_LINHA1.4
/PC3: CN9.6, SENSOR_LINHA1.5
/PC8: BOTAO1.2, CN8.1
/PC9: CN8.3, RFID.6
/PC10: CN8.5, RFID.4
/PC11: CN8.7, RFID.3
/PC12: CN8.9, RFID.2
/PD0: CN9.26, CON_LIVRE1.5
/PD1: CN9.28, CON_LIVRE1.6
/PD2: CN8.11, RFID.1
/PD14: CN7.15, DRIVER_MOTOR1.3
/PD15: CN7.17, DRIVER_MOTOR1.2
/PE2: CN9.13, CN10.26
/PE3: CN9.21, CON_LIVRE2.5
/PE5: CN9.17, CON_LIVRE2.7
/PE6: CN9.19, CON_LIVRE2.6
/PF0: CN9.22, CON_LIVRE1.3
/PF1: CN9.20, CON_LIVRE1.2
/PF2: CN9.18, CON_LIVRE1.1
/PF3: CN9.8, SENSOR_LINHA1.6
/PF5: CN9.10, SENSOR_LINHA1.7
/PF7: CN9.25, CON_LIVRE2.3
/PF8: CN9.23, CON_LIVRE2.4
/PF9: CN9.27, CON_LIVRE2.2
/PF10: CN9.12, SENSOR_LINHA1.8
/PG0: CN9.30, CON_LIVRE1.7
/PG1: CN9.29, CON_LIVRE2.1
GND: BOTAO1.1, CN7.7, CN8.12, CN8.14, CN9.11, CN9.24, CN10.6, CN10.18, CN10.21, CN10.28, CON_LIVRE1.4, C_BLUE1.2, C_RFID1.2, C_SLINHA1.2, C_SOBST1.2, DRIVER_MOTOR1.1, Fonte3.3V1.1, Fonte3.3V1.5, Fonte5V1.1, Fonte5V1.5, RFID.7, SENSOR_LINHA1.1, SENSOR_OBSTACULOS1.2, bluetooth1.4

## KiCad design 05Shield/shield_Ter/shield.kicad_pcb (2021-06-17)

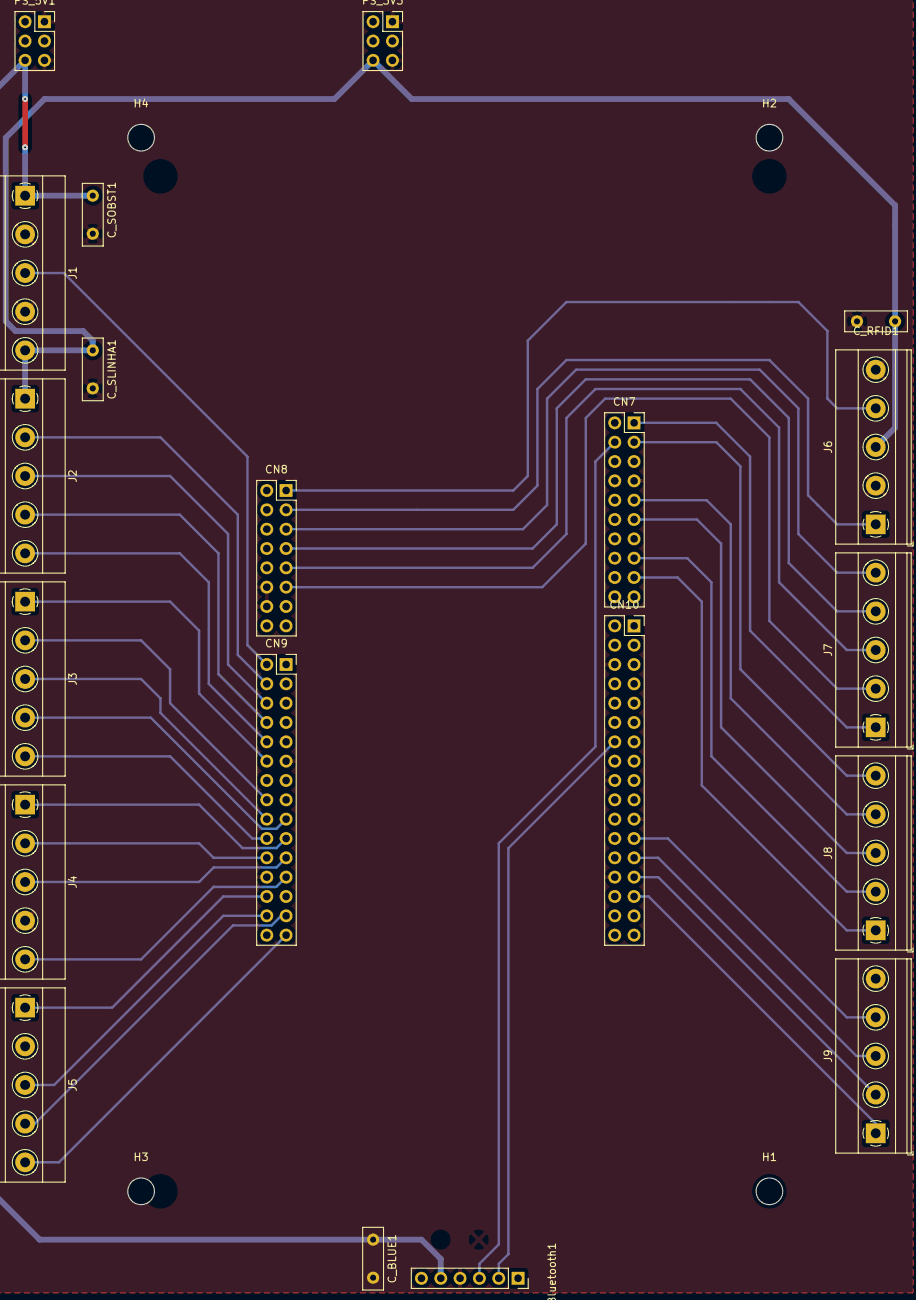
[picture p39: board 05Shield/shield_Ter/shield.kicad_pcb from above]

Board: 2 copper layers, 24 parts (0 on the bottom side), 42 nets.

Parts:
Bluetooth1: Conn_01x06; PinSocket_1x06_P2.54mm_Vertical
CN7: Conn_02x10_Odd_Even; PinSocket_2x10_P2.54mm_Vertical
CN8: Conn_02x08_Odd_Even; PinSocket_2x08_P2.54mm_Vertical
CN9: Conn_02x15_Odd_Even; PinSocket_2x15_P2.54mm_Vertical
CN10: Conn_02x17_Odd_Even; PinSocket_2x17_P2.54mm_Vertical
C_BLUE1: C; C_Disc_D8.0mm_W2.5mm_P5.00mm
C_RFID1: C; C_Disc_D8.0mm_W2.5mm_P5.00mm
C_SLINHA1: C; C_Disc_D8.0mm_W2.5mm_P5.00mm
C_SOBST1: C; C_Disc_D8.0mm_W2.5mm_P5.00mm
H1, H2, H3, H4: MountingHole; MountingHole_3.5mm
J1, J2, J3, J4, J5: Screw_Terminal_01x05; TerminalBlock_Phoenix_MKDS-1,5-5-5.08_1x05_P5.08mm_Horizont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
J6, J7, J8, J9: Screw_Terminal_01x04; TerminalBlock_Phoenix_MKDS-1,5-5-5.08_1x05_P5.08mm_Horizont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
PS_3V3, PS_5V1: Screw_Terminal_02x03; PinSocket_2x03_P2.54mm_Vertical

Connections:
+3V3: C_RFID1.1, C_SLINHA1.1, J1.5, J2.1, J6.3, PS_3V3.2, PS_3V3.6
+5V: Bluetooth1.5, C_BLUE1.1, C_SOBST1.1, J1.1, PS_5V1.2, PS_5V1.6
AVDD: CN7.5, CN10.2
GND: Bluetooth1.4, CN7.7, CN8.12, CN8.14, CN9.11, CN9.24, CN10.6, CN10.18, CN10.21, CN10.28, C_BLUE1.2, C_RFID1.2, C_SLINHA1.2, C_SOBST1.2, J1.2, J1.4, J4.4, J6.2, J6.5, J9.5, PS_3V3.1, PS_3V3.5, PS_5V1.1, PS_5V1.5
NC: CN8.2, CN9.14
PA3: CN9.2, J1.3
PA5: CN7.9, J8.4
PA6: CN7.11, J8.3
PA7: CN7.13, CN9.16, J3.2
PB6: Bluetooth1.2, CN10.14
PB8: CN7.1, J7.1
PB9: CN7.3, J8.5
PB15: Bluetooth1.3, CN7.4
PC0: CN9.4, J2.2
PC3: CN9.6, J2.3
PC8: CN8.1, J6.4
PC9: CN8.3, J6.1
PC10: CN8.5, J7.5
PC11: CN8.7, J7.4
PC12: CN8.9, J7.3
PD0: CN9.26, J5.1
PD1: CN9.28, J5.3
PD2: CN8.11, J7.2
PD14: CN7.15, J8.2
PD15: CN7.17, J8.1
PE2: CN9.13, CN10.26
PE3: CN9.21, J4.3
PE5: CN9.17, J3.4
PE6: CN9.19, J4.1
PE10: CN10.23, J9.4
PE12: CN10.25, J9.3
PE14: CN10.27, J9.2
PE15: CN10.29, J9.1
PF0: CN9.22, J4.2
PF1: CN9.20, J3.5
PF2: CN9.18, J3.3
PF3: CN9.8, J2.4
PF5: CN9.10, J2.5
PF8: CN9.23, J4.5
PF9: CN9.27, J5.4
PF10: CN9.12, J3.1
PG1: CN9.29, J5.5

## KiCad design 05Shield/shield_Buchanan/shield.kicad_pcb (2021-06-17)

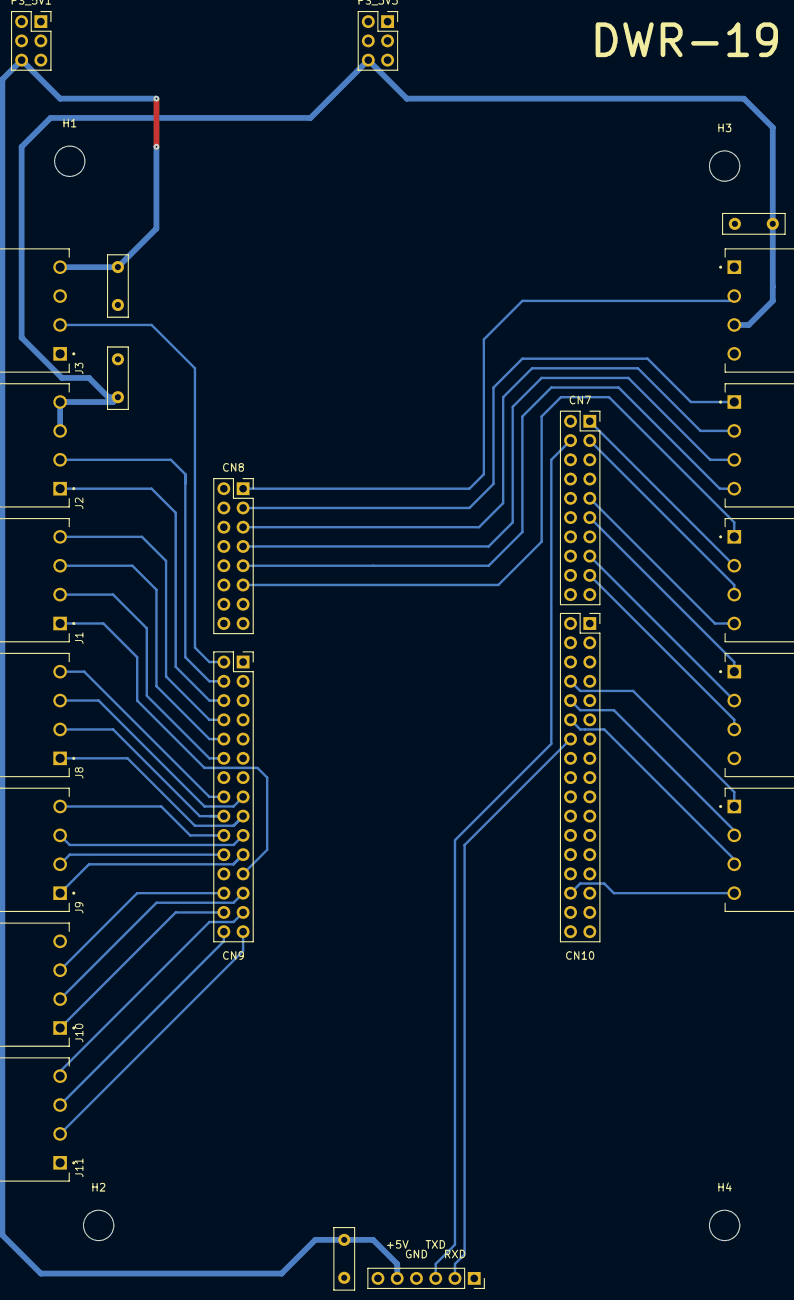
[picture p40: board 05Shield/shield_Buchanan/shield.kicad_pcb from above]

Board: 2 copper layers, 27 parts (0 on the bottom side), 45 nets.

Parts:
Bluetooth1: Conn_01x06; PinSocket_1x06_P2.54mm_Vertical
CN7: Conn_02x10_Odd_Even; PinSocket_2x10_P2.54mm_Vertical
CN8: Conn_02x08_Odd_Even; PinSocket_2x08_P2.54mm_Vertical
CN9: Conn_02x15_Odd_Even; PinSocket_2x15_P2.54mm_Vertical
CN10: Conn_02x17_Odd_Even; PinSocket_2x17_P2.54mm_Vertical
C_BLUE1: C; C_Disc_D8.0mm_W2.5mm_P5.00mm
C_RFID1: C; C_Disc_D8.0mm_W2.5mm_P5.00mm
C_SLINHA1: C; C_Disc_D8.0mm_W2.5mm_P5.00mm
C_SOBST1: C; C_Disc_D8.0mm_W2.5mm_P5.00mm
H1, H2, H3, H4: MountingHole; MountingHole_4mm
J1, J2, J3, J4, J5, J6, J7, J8, J9, J10, J11, J12: Screw_Terminal_01x04; TE_284513-4
PS_3V3, PS_5V1: Screw_Terminal_02x03; PinSocket_2x03_P2.54mm_Vertical

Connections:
+3V3: C_RFID1.1, C_SLINHA1.1, J2.3, J2.4, J7.3, PS_3V3.2, PS_3V3.6
+5V: Bluetooth1.5, C_BLUE1.1, C_SOBST1.1, J3.4, PS_5V1.2, PS_5V1.6
AVDD: CN7.5, CN10.2
GND: Bluetooth1.4, CN7.7, CN8.12, CN8.14, CN9.11, CN9.24, CN10.6, CN10.18, CN10.21, CN10.28, C_BLUE1.2, C_RFID1.2, C_SLINHA1.2, C_SOBST1.2, J3.1, J3.3, J4.4, J7.1, J7.4, J10.4, PS_3V3.1, PS_3V3.5, PS_5V1.1, PS_5V1.5
NC: CN8.2, CN9.14
PA0: CN10.30, J12.4
PA3: CN9.2, J3.2
PA5: CN7.9, J5.4
PA6: CN7.11, J4.1
PA7: CN7.13, CN9.16, J8.4
PB1: CN10.8, J12.1
PB6: Bluetooth1.2, CN10.14
PB8: CN7.1, J5.2
PB9: CN7.3, J5.3
PB15: Bluetooth1.3, CN7.4
PC0: CN9.4, J2.2
PC2: CN10.10, J12.2
PC3: CN9.6, J2.1
PC8: CN8.1, J7.2
PC9: CN8.3, J6.1
PC10: CN8.5, J6.2
PC11: CN8.7, J6.3
PC12: CN8.9, J6.4
PD0: CN9.26, J10.3
PD1: CN9.28, J10.1
PD2: CN8.11, J5.1
PD14: CN7.15, J4.2
PD15: CN7.17, J4.3
PE2: CN9.13, CN10.26
PE3: CN9.21, J9.1
PE4: CN9.15, J8.3
PE5: CN9.17, J8.1
PE6: CN9.19, J9.3
PF0: CN9.22, J9.2
PF1: CN9.20, J9.4
PF2: CN9.18, J8.2
PF3: CN9.8, J1.4
PF4: CN10.12, J12.3
PF5: CN9.10, J1.3
PF7: CN9.25, J10.2
PF8: CN9.23, J1.1
PF9: CN9.27, J11.4
PF10: CN9.12, J1.2
PG0: CN9.30, J11.3
PG1: CN9.29, J11.2

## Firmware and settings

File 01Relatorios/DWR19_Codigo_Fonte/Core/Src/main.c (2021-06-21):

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
/* Includes ------------------------------------------------------------------*/
#include "main.h"
#include "adc.h"
#include "dma.h"
#include "spi.h"
#include "tim.h"
#include "usart.h"
#include "gpio.h"

/* USER CODE BEGIN Includes */
#include "fsm.h"
#include "tests.h"

#include "rfid-rc522.h"
#include "debounce.h"
#include "timeout.h"
/* USER CODE END Includes */


void SystemClock_Config(void);
/**
  * @brief  The application entry point.
  * @retval int
  */
int main(void)
{
  /* MCU Configuration--------------------------------------------------------*/

  /* Reset of all peripherals, Initializes the Flash interface and the Systick. */
  HAL_Init();

  /* Configure the system clock */
  SystemClock_Config();

  /* Initialize all configured peripherals */
  MX_GPIO_Init();
  MX_DMA_Init();
  MX_SPI3_Init();
  MX_USART3_UART_Init();
  MX_TIM6_Init();
  MX_ADC3_Init();
  MX_TIM4_Init();
  MX_USART1_UART_Init();
  MX_TIM3_Init();
  MX_ADC2_Init();
  MX_TIM7_Init();
  /* Infinite loop */
  /* USER CODE BEGIN WHILE */

  // initialize FSM state and next state
  state = S_STOPPED;
  nstate = S_STOPPED;

  // enable RFID reader
  RFID_RC522_Init();
  // enable UART
  Rx_UART_init(&bluet_uart);
  // initialize debounce button
  debounce_start(&button, USER_BTN_PORT, USER_BTN_PIN);

  // enable timeouts
  timeout_start();

  while (1)
  {
	  // execute state
	  fsm_func_ptr[state]();
	  // update current state
	  state = nstate;

    /* USER CODE END WHILE */

    /* USER CODE BEGIN 3 */
  }
  /* USER CODE END 3 */
}

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


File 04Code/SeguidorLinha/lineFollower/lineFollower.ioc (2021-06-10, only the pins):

PG6.Signal=GPIO_Output
Mcu.UserName=STM32F767ZITx
PB14.GPIO_Label=LD3 [Red]
PG6.GPIO_Label=USB_PowerSwitchOn [STMPS2151STR_EN]
PA14.GPIO_Label=TCK
PC0.GPIO_Label=SENSOR1
PC6.GPIO_Label=PWN_RIGHT
PC13.GPIO_Label=USER_Btn [B1]
PB13.GPIO_Label=IN2_RIGHT
PB11.Signal=GPIO_Output
PB13.Signal=GPIO_Output
PB15.Signal=GPIO_Output
PA15.GPIO_Label=IN2_LEFT
PC7.Signal=S_TIM3_CH2
PC3.Signal=ADCx_IN13
PD8.Signal=USART3_TX
PB12.GPIO_Label=IN1_LEFT
PB7.Signal=GPIO_Output
PF3.Signal=ADC3_IN9
PB7.GPIO_Label=LD2 [Blue]
PA15.Signal=GPIO_Output
PF5.Signal=ADC3_IN15
PG7.Signal=GPIO_Input
PC13.Signal=GPXTI13
PC6.Signal=S_TIM3_CH1
PB11.GPIO_Label=TESTE
PD9.Signal=USART3_RX
PC0.Signal=ADCx_IN10
PA13.Signal=SYS_JTMS-SWDIO
PB14.Signal=GPIO_Output
PB15.GPIO_Label=IN1_RIGHT
PG7.GPIO_Label=USB_OverCurrent [STMPS2151STR_FAULT]
PF10.Signal=ADC3_IN8
PC7.GPIO_Label=PWM_LEFT
PA7.GPIO_Label=SENSOR8
PA14.Signal=SYS_JTCK-SWCLK
PB0.Signal=GPIO_Output
PB12.Signal=GPIO_Output
PA7.Signal=ADCx_IN7

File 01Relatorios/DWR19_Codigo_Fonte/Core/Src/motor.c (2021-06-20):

/*
 * motor.c
 *
 * Motor control module
 *
 *  Created on: May 5, 2021
 */
#include "motor.h"
#include "tim.h" // using set_pwm()

/******************************************************************************
Motor Init

@brief	Start PWM generation to a given motor
@param	Motor to be initialized
@retval none
******************************************************************************/
void motor_init(motor_st *m)
{
	HAL_TIM_PWM_Start(m->htim, m->pwm_channel);
}

/******************************************************************************
Motor Kill

@brief	Stops PWM generation to a given motor
@param	Motor to be killed
@retval none
******************************************************************************/
void motor_kill(motor_st *m)
{
	HAL_TIM_PWM_Stop(m->htim, m->pwm_channel);
	// disable IN pins
	motor_control(m,  0, MOTOR_STOP);
}

/******************************************************************************
Define motor GPIO Pins config according to each direction
******************************************************************************/
static const GPIO_PinState motor_pin_config[3][2] =
{
		// Motor BACKWARD
		{GPIO_PIN_RESET, GPIO_PIN_SET},
		// Motor FORWARD
		{GPIO_PIN_SET, GPIO_PIN_RESET},
		// Motor STOP
		{GPIO_PIN_RESET, GPIO_PIN_RESET}
};

/******************************************************************************
Motor control

@brief	Controls Motor PWM duty cycle in desired direction
@param	Motor to be controlled
		New PWM duty cycle
		Direction of motor rotation
@retval none
******************************************************************************/
void motor_control(motor_st *m,  uint8_t dc, motor_dir_e dir)
{
	// Write motor GPIO Pin1
	HAL_GPIO_WritePin(m->GPIO_port_IN1, m->GPIO_pin_IN1, motor_pin_config[dir][0]);
	// Write motor GPIO Pin1
	HAL_GPIO_WritePin(m->GPIO_port_IN2, m->GPIO_pin_IN2, motor_pin_config[dir][1]);
	// Set/Update motor PWM duty cycle
	set_pwm(m->htim, m->pwm_channel, dc);
}

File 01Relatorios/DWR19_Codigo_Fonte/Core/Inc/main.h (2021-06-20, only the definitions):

#define SENSOR4_Pin GPIO_PIN_3
#define SENSOR4_GPIO_Port GPIOF
#define SENSOR5_Pin GPIO_PIN_5
#define SENSOR5_GPIO_Port GPIOF
#define SENSOR8_Pin GPIO_PIN_8
#define SENSOR8_GPIO_Port GPIOF
#define SENSOR6_Pin GPIO_PIN_10
#define SENSOR6_GPIO_Port GPIOF
#define SENSOR1_Pin GPIO_PIN_0
#define SENSOR1_GPIO_Port GPIOC
#define SENSOR3_Pin GPIO_PIN_3
#define SENSOR3_GPIO_Port GPIOC
#define OBS_DETECTOR_Pin GPIO_PIN_3
#define OBS_DETECTOR_GPIO_Port GPIOA
#define IN2_RIGHT_Pin GPIO_PIN_5
#define IN2_RIGHT_GPIO_Port GPIOA
#define IN1_LEFT_Pin GPIO_PIN_6
#define IN1_LEFT_GPIO_Port GPIOA
#define DEBUG_LGREEN_Pin GPIO_PIN_0
#define DEBUG_LGREEN_GPIO_Port GPIOB
#define BUZZER_Pin GPIO_PIN_1
#define BUZZER_GPIO_Port GPIOB
#define DEBUG_LRED_Pin GPIO_PIN_14
#define DEBUG_LRED_GPIO_Port GPIOB
#define BLUET_RX_Pin GPIO_PIN_15
#define BLUET_RX_GPIO_Port GPIOB
#define IN2_LEFT_Pin GPIO_PIN_14
#define IN2_LEFT_GPIO_Port GPIOD
#define PWM_LEFT_Pin GPIO_PIN_15
#define PWM_LEFT_GPIO_Port GPIOD
#define USER_BTN_Pin GPIO_PIN_8
#define USER_BTN_GPIO_Port GPIOC
#define SPI3_SDA_Pin GPIO_PIN_2
#define SPI3_SDA_GPIO_Port GPIOD
#define BLUET_TX_Pin GPIO_PIN_6
#define BLUET_TX_GPIO_Port GPIOB
#define DEBUG_LBLUE_Pin GPIO_PIN_7
#define DEBUG_LBLUE_GPIO_Port GPIOB
#define PWM_RIGHT_Pin GPIO_PIN_8
#define PWM_RIGHT_GPIO_Port GPIOB
#define IN1_RIGHT_Pin GPIO_PIN_9
#define IN1_RIGHT_GPIO_Port GPIOB

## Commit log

2021-03-08 Added working time table
    [DiagramaGantt.xlsx, WorkingTime.xlsx]
2021-03-10 planeamento acabado
    [DiagramaGantt.xlsx]
2021-03-11 Added components
    [LogBook.xlsx, WorkingTime.xlsx]
2021-03-15 Starting Etapa1
    [LogBook.xlsx]
2021-03-18 Etapa1 done
    [LogBook.xlsx]
2021-03-29 Logbook update
    [LogBook.xlsx]
2021-03-31 read sensor values with DMA
2021-03-31 Added stop mark sensor Flowchart
    [LogBook.xlsx]
2021-03-31 Added obstacles sensor flowchart
    [LogBook.xlsx]
2021-04-01 Sensors readme update
2021-04-01 Joao/Duarte update logbook -> day 31/03
    [LogBook.xlsx]
2021-04-14 Added RFID code, Updated logbook and components list
    [LogBook.xlsx]
2021-05-04 Logbook yesterday
    [LogBook.xlsx]
2021-05-05 Added documentation
    [ObstacleSensor.xlsx]
2021-05-05 Detectors debug
    [LogBook.xlsx, ObstacleSensor.xlsx]
2021-05-05 add seguidor de linha
2021-05-05 update RFID module
    [LogBook.xlsx]
2021-06-01 Working on Stop Sensors
    [ObstacleSensor.xlsx]
2021-06-02 qtr dma
2021-06-03 Controlador PID feito (valores Kp,Ki,Kd escolhidos) | diagrama PID
2021-06-03 Stop sensors done
2021-06-04 Added battery schema
2021-06-05 little changes on PID algorithm
2021-06-06 update log book
    [LogBook.xlsx]
2021-06-07 Working on PID
2021-06-07 Updated Logbook and added Perifericos
    [LogBook.xlsx, Perifericos.xlsx]
2021-06-08 some corrections line top speed. Not working anyway
    [lfollower.c, main.c, move.c]
2021-06-08 Revert "Updated Logbook and added Perifericos"
    This reverts commit dbdd964fc060a66478d0325b46005da320524534.
    [Perifericos.xlsx]
2021-06-08 pin excel v1
    [Perifericos.xlsx]
2021-06-08 perifericos updat
    e
    [Perifericos.xlsx]
2021-06-08 edit pinout excel, add pinout kicad
    [Infineon_PG-LLGA-5-1.FCStd, L_Coilcraft_LPS5030.FCStd, L_Wuerth_WE-TPC-3816.FCStd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]
2021-06-09 line sensor 6 adc
2021-06-09 Testing stop sensors
    [LogBook.xlsx]
2021-06-09 errors detected: lacks 'lf_rotate' from lineFollower
    [adc.c, fsm.c, fsm.ioc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]
2021-06-09 shield 7 ADCs e perifericos
    [Infineon_PG-LLGA-5-1.FCStd, L_Coilcraft_LPS5030.FCStd, L_Wuerth_WE-TPC-3816.FCStd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]
2021-06-09 Cleaned RFID.c (only SPI3 folder)
    Won't modify SPI1 RFID to in order to keep a backup
    [rfid-rc522.c]
2021-06-09 Added Diagramas
    [Diagrama_Robo_v3.dwg]
2021-06-10 pcb conetores demasiado caros
    [284513-4.step, Infineon_PG-LLGA-5-1.FCStd, L_Coilcraft_LPS5030.FCStd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]
2021-06-10 PCB with Aquario con
    [shield.kicad_pcb, shield.sch]
2021-06-10 Corrected PCB
    [shield.kicad_pcb]
2021-06-10 PCB ready with buchanan conectors
    [284513-4.step, shield.kicad_pcb, shield.sch]
2021-06-10 texto maquina de estados
2021-06-10 Update PCB with new pins -> ADC3
    [shield.kicad_pcb, shield.sch]
2021-06-10 pcb adc 3
    [shield.kicad_pcb, shield.sch]
2021-06-10 PID text uptade
2021-06-10 Update PID and State Machine text
2021-06-10 Test stop sensors
2021-06-11 Updated Diagrams
    [Diagrama_Robo_v3.dwg]
2021-06-11 last update Kicad
    [shield.kicad_pcb, shield.sch]
2021-06-11 word pid
2021-06-12 pid word update
2021-06-12 PID followchart upadate. Word update
2021-06-12 Rellocated timers. Timeout timer max 140sec
2021-06-13 logbook components
    [LogBook.xlsx]
2021-06-13 Buracos 4mm
    [shield.kicad_pcb, shield.sch]
2021-06-13 Ficheiros Gerber!
    [shield-B_Cu.gbr, shield-B_Mask.gbr, shield-B_Paste.gbr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]
2021-06-14 atulizaçao do logbook | lista de componentes | ordem de trabalhos
    [LogBook.xlsx]
2021-06-14 DMA (pouca coisa)
2021-06-14 pid completed - no review done
2021-06-15 PID Word update (Offset explained)-> no review
2021-06-15 DMA acabado
2021-06-15 circuitos de alimentacao update
2021-06-15 Diagrams Updated
    [Diagrama_Robo_v3.dwg]
2021-06-15 circuito mecanico - 1 review
2021-06-15 correcao PID adc diagrama
2021-06-15 DMA -> EN
2021-06-16 relatorio - timers
2021-06-16 Uart added and small fixes to spi
2021-06-16 Updated Diagrams (~98% done)
    [Diagrama_Robo_v3.dwg]
2021-06-16 Diagrams 99% done - pdf preview available
    Still needs front sensor
    [Diagrama_Robo_v3.dwg]
2021-06-16 comentarios e possiveis correcoes SPI
2021-06-16 UART possiveis correcoes
2021-06-16 atualização do SPI | inicio da tabela de perifericos
2021-06-16 mudança da pasta da shield
    [284513-4.step, Infineon_PG-LLGA-5-1.FCStd, L_Coilcraft_LPS5030.FCStd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]
2021-06-16 Completed Mechanical Diagrams
    [Diagrama_Robo_v3.dwg]
2021-06-17 Tabelas de perifericos
2021-06-18 Added sensores
2021-06-18 DMA e ADC corrigido e adicionado ao relatorio
2021-06-18 Updated diagrams (3D Model)
    [Diagrama_Robo_v3.dwg, RFID connections.dwg]
2021-06-18 Corrected UART and merged it with Perifericos
    Still needs tables
2021-06-18 Corrected and Merged SPI to Perifericos
    Still needs configuration table
2021-06-18 Diagrama PID corrigido
2021-06-18 Review fsm pid
2021-06-18 mais uma correcao diagrama PID
2021-06-18 Review pid
2021-06-18 UART and SPI
2021-06-18 Create STM32 e Shield.docx
2021-06-18 Fluxograma PID corrigido
2021-06-18 Diagrama PID alteradoQ
2021-06-19 PID + CAlimentacao + PCB(Shield)
    [Perifericos.xlsx]
2021-06-19 Upadated 3D model
    Added RFID support and side button. Missing switch, charging port and obstacle sensor.
    [Diagrama_Robo_v3.dwg, Diagrama_Robo_v3.stl]
2021-06-19 parte mecanica e de software adicionada ao Relatorio
2021-06-19 diagrama de Gantt e relatorio (falta rever)
    [DiagramaGantt.xlsx]
2021-06-20 alteracoes ao DMA ADC e timers
2021-06-20 mapeamento de memoria
    [Perifericos.xlsx]
2021-06-20 RE do PID e motores
2021-06-20 Alteracoes relatorio DMA
2021-06-21 Removed unnecessary files
    [284513-4.step, Infineon_PG-LLGA-5-1.FCStd, L_Coilcraft_LPS5030.FCStd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]
2021-06-21 Finished 3D model
    [Diagrama_Robo_v3.dwg, Diagrama_Robo_v3.stl]
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2021-06-21 correct pid values in relatorio
2021-06-22 Added LeSpeciale
    Nem acredito que gastei 4 horas nisto. Não acrescentei o pdf para não dar arruinar a surpresa.
    [Diagrama_Robo_v3.dwg, LeSpeciale.dwg]
2021-06-22 Update LeSpeciale
    Y tho?
    [LeSpeciale.dwg]

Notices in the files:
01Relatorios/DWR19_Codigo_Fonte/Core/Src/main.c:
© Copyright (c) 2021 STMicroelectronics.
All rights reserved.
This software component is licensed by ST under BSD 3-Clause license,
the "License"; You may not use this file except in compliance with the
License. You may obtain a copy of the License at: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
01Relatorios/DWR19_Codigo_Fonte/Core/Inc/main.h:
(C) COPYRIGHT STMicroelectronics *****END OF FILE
